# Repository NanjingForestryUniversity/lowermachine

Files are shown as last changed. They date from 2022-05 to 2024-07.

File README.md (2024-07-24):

# 下位机

下位机按上位机指令根据传送带脉冲等触发相机，完成棉花异性纤维的分选任务。采用的硬件是[Alinx](https://www.alinx.com/)的AC7Z100C ZYNQ开发板。

本IO扩展版提供了

- xxxxxx

接线时，12V电源连接到IO扩展板的电源接口，相机线应连接相机触发接口`TRIG1`、`TRIG2`和对应的`GND`接口，编码器线应连接在编码器输入接口`E1`和对应的`GND`接口，物体传感器应连接输入接口`E3`和对应的`GND`接口。注意底板不连接任何外部电源。

开发和部署说明见[doc/develop_and_deploy.md](doc/develop_and_deploy.md)

## 目录结构

- doc为说明文档，包括开发和部署细节、硬件设计的描述等

  - [develop_and_deploy.md](doc/develop_and_deploy.md)为开发和部署说明，首先看这个文档
  - [hardware_description.md](doc/hardware_description.md)为PL端逻辑设计说明，阐述了硬件工作的整体流程
  - [pl_reference_mannual.md](doc/pl_reference_mannual.md)为PL端逻辑在AXI总线上映射的寄存器参考手册
  - [sim_uppermachine_manual.md](doc/sim_uppermachine_manual.md)为模拟上位机运行的参考手册

- script为配置系统、安装环境、安装可执行文件、卸载可执行文件等的脚本

  关于脚本的使用，见[doc/develop_and_deploy.md](doc/develop_and_deploy.md)

  - target.sh为嵌入式linux中自动启动应用程序脚本

  - load\*.sh为嵌入式linux中加载驱动的脚本
  - .bashrc为嵌入式linux中配置环境变量的脚本

- protocol为上位机和下位机通信的协议

- hardware下位机主板、接口板、底板等的硬件设计

  - pl_platform为PL端硬件设计
  - xme0724ioextend为IO叠板的原理图和PCB

- source为AC7Z100C板子上运行的源程序和模拟上位机程序

  - liunx_app为Linux上运行的应用程序，即业务逻辑
  - linux_driver为Linux上的驱动，用于控制自定义的PL端硬件，其中drv_test结尾的目录为相应驱动模块的测试应用程序
  - petalinux_config为petalinux工具在编译u-boot、kernel、rootfs前进行的配置
  - petalinux_devicetree为本次自定义的Linux设备树文件部分，其余设备树为自动生成的
  - petalinux_hwdescription为petalinux所使用的硬件描述文件，包含了vivado工程中的比特流等信息
  - sim_uppermachine_manul为基于pyside6所编写的软件，用于模拟上位机发送指令，方便调试

## 版本

由于经常有不同类型的新要求出现，比如分选糖果、分选烟梗、同为糖果也具有不同的参数，因此不同的下位机型号（注意不是更新，比如同一台机器需要设置新的参数）应建立不同的分支，**主分支无实际意义**

分支命名规则（不使用中文，小写无空格）

```shell
b分支编号-p生产环境项目名-t分选对象[-其他特点1[-其他特点2...]]
```

中括号在这里表示可省略的项，中括号本身不应出现在实际命名中，其他特点应字母打头，可有多个，"-"相连

使用Git的tag功能定义版本（注意连着tag一起push），Github仓库的release功能同步发布最新版本

版本号遵循定义如下（不使用中文，小写无空格）

```shell
b分支编号-d文档版本-hPCB设计版本-lFPGA设计版本-p协议版本-s脚本版本-aAPP代码版本-i驱动版本-c系统编译配置版本-e设备树版本
```

分支编号和分支命名中编号一致。各部分版本应在相应目录下创建文件注明，比如`2.1`版本的PCB设计：PCB工程目录中建立`version`文本文件，内容为文本`2.1`。对于涉及整体设计的大改动版本号加`1`，其余改动版本号加`0.1`。每个分支的版本各自独立，新分支的版本从`1.0`起计算，也可从建立分支处原有版本起计算

##  作者

作者徐耀，随时欢迎师弟师妹7x24提着示波器的来问问题，联系方式：QQ：1170701029；微信：CeRnYool。

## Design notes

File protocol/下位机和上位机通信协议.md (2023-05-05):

# 下位机和上位机通信协议 V1.4

工作在OSI5~7层，单播TCP/IP。下位机控制阀，为客户端；上位机负责识别，为服务端

- 灵活利用类型字段实际值区分数据和指令
- 安全高效的长度定义，应对TCP/IP分粘包特性
- 字符序列形式简洁直观，方便抓包调试

## 流程

下位机上电后40s完成启动，初始处于停止状态。

要开始分选，下位机应处于停止状态，上位机先设置各个相机触发周期对应的编码器脉冲数，然后发送开始分选指令

收到开始分选指令后，下位机进入正在分选状态，依据编码器脉冲和设定，触发相机拍摄

上位机发送停止分选指令时，下位机应处于正在分选状态，下位机收到后停止读入编码器脉冲和触发相机，并进入停止状态。停止状态下下位机忽略收到的喷阀数据

## 格式

一包数据由8'haa打头，8'hbb结束，共6个字段：

| 起始  | 长度1 | 长度2 | 长度3 | 长度4 | 类型1 | 类型2 | 数据1 | 数据2 | ...  | 数据$i$ | 校验1 | 校验2 | 结束  |
| :---: | :---: | :---: | :---: | :---: | :---: | :---: | :---: | :---: | :--: | :-----: | :---: | :---: | :---: |
| 8'haa | 8'hzz | 8'hzz | 8'hzz | 8'hzz | 8'hzz | 8'hzz | 8'hzz | 8'hzz | ...  |  8'hzz  | 8'hff | 8'hff | 8'hbb |

### 起始&结束

起始为1字节，8'haa；结束为1字节，8'hbb

### 校验&长度

校验为2字节，`校验1`为8'hff，`校验2`为8'hff

长度为一个32位无符号数length，长度 = 数据字节数$i + 2$ <br>`长度1`指length[31:24]，`长度2`指length[23:16]，`长度3`指length[15:8]，`长度4`指length[7:0]

### 类型&数据

类型为ASCII字符序列，比如`类型1`为's'，`类型2`为't'代表开始分选命令<br>数据为ASCII字符序列或原始数据

**开始分选指令**<br>`类型1`为's'，`类型2`为't'，length为3，数据1固定为8'hff，具体如下：

| 起始  | 长度1 | 长度2 | 长度3 | 长度4 | 类型1 | 类型2 | 数据1 | 校验1 | 校验2 | 结束  |
| :---: | :---: | :---: | :---: | :---: | :---: | :---: | :---: | :---: | :---: | :---: |
| 8'haa | 8'd0  | 8'd0  | 8'd0  | 8'd3  |  's'  |  't'  | 8'hff | 8'hff | 8'hff | 8'hbb |

**停止分选指令**<br>`类型1`为's'，`类型2`为'p'，length为3，数据固定为8'hff，具体如下：

| 起始  | 长度1 | 长度2 | 长度3 | 长度4 | 类型1 | 类型2 | 数据1 | 校验1 | 校验2 | 结束  |
| :---: | :---: | :---: | :---: | :---: | :---: | :---: | :---: | :---: | :---: | :---: |
| 8'haa | 8'd0  | 8'd0  | 8'd0  | 8'd3  |  's'  |  'p'  | 8'hff | 8'hff | 8'hff | 8'hbb |

**设置相机触发周期对应的编码器脉冲数**<br>对于相机a，`类型1`为'p'，`类型2`为'a'，length为10，数据为十进制的ASCII字符序列，不足补'0'，比如'0''0''0''0''0''2''3''1'表示每231个编码器脉冲触发一次相机：

| 起始  | 长度1 | 长度2 | 长度3 | 长度4 | 类型1 | 类型2 | 数据1 | ...  | 数据7 | 数据8 | 校验1 | 校验2 | 结束  |
| ----- | ----- | ----- | ----- | ----- | ----- | ----- | ----- | ---- | ----- | ----- | ----- | ----- | ----- |
| 8'haa | 8'd0  | 8'd0  | 8'd0  | 8'd10 | 'p' | 'a' | '0' | ...  | '3' | '1' | 8'hff | 8'hff | 8'hbb |

对于相机b，`类型1`为'p'，`类型2`为'b'，其余字节含义和用法与相机a一致

对于相机c，`类型1`为'p'，`类型2`为'c'，其余字节含义和用法与相机a一致

对于相机d，`类型1`为'p'，`类型2`为'd'，其余字节含义和用法与相机a一致

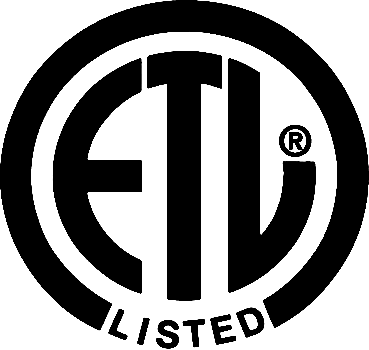
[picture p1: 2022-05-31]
hardware/ac7z100cioextend/res/etl.png

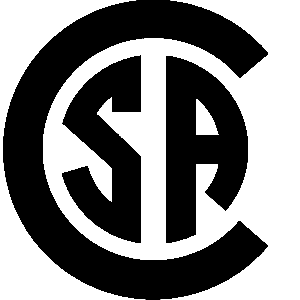
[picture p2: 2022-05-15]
hardware/ac7z100cioextend/res/csa.png

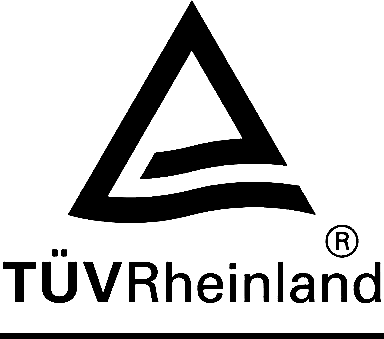
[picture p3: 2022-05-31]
hardware/ac7z100cioextend/res/tuv.png

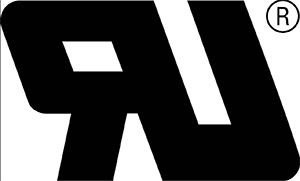
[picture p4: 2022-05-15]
hardware/ac7z100cioextend/res/ul.png

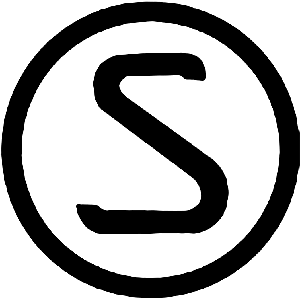
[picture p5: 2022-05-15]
hardware/ac7z100cioextend/res/semko.png

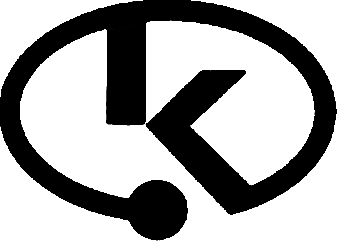
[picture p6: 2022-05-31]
hardware/ac7z100cioextend/res/ekmark.png

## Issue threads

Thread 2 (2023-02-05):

糖果分选机开始分选后传送带变速打不准

3703781, 2023-02-05:
这个版本[b01-d0.1-h1.0-p1.0-s0.1-a1.0](https://github.com/NanjingForestryUniversity/lowermachine/tree/b01-d0.1-h1.0-p1.0-s0.1-a1.0)
糖果分选机开始分选后传送带变速打不准
下面是维尔斯卢工的原话：
> 慢速调到能打了，做标记。调节到最快，打不到，再调到原先的慢速，也打不到，打的位置和快速一样的位置。停止分选，再开始分选，又能打到了。再调快打不准，再回原位也打不准，必须再停，再开。

3703781, 2023-02-05:
2023.02.06 过奕任、程磊、薛胜、吴旻会到维尔斯出差解决

3703781, 2023-02-08:
原因是传送带速度太快，相机触发频率较高，上位机算法不能及时计算出结果
在这个版本[b01-d0.2-h1.1-p1.0-s1.0-a1.1](https://github.com/NanjingForestryUniversity/lowermachine/tree/b01-d0.2-h1.1-p1.0-s1.0-a1.1)中，当存储上位机的图像数据队列为空时，将会给上位机发送报错信息。上位机收到后可以重新开始分选。同时让卢工固定传送带速度到约1m/s。

Chenglei98, 2023-02-08:
收到，miaow

&nbsp;

------------------&nbsp;原始邮件&nbsp;------------------
发件人:                                                                                                                        "NanjingForestryUniversity/lowermachine"                                                                                    ***@***.***&gt;;
发送时间:&nbsp;2023年2月8日(星期三) 晚上9:06
***@***.***&gt;;
***@***.******@***.***&gt;;
主题:&nbsp;Re: [NanjingForestryUniversity/lowermachine] 糖果分选机开始分选后传送带变速打不准 (Issue #2)

原因是传送带速度太快，相机触发频率较高，上位机算法不能及时计算出结果
 在这个版本b01-d0.2-h1.1-p1.0-s1.0-a1.1中，当存储上位机的图像数据队列为空时，将会给上位机发送报错信息。上位机收到后可以重新开始分选。同时让卢工固定传送带速度到约1m/s。

—
Reply to this email directly, view it on GitHub, or unsubscribe.
You are receiving this because you were assigned.Message ID: ***@***.***&gt;

Closed 2023-02-08.

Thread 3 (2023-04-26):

关于刘英老师的刨花板缺陷检测和分选

laiyz11, 2023-04-26:
刘老师的刨花板项目需要我们进行相机触发以及使用光电开关检测是否有木板在拍摄区域，具体要求是：
有木板在拍摄区域则需要依据编码器脉冲触发相机拍摄；
如果没有木板在拍摄区域则停止相机的触发脉冲；
需要同时触发多台相机

3703781, 2023-04-26:
已经新建分支 [b03-pwoodsorting-tchipboard1](https://github.com/NanjingForestryUniversity/lowermachine/tree/b03-pwoodsorting-tchipboard1)，用于这个项目

Closed 2023-04-28.

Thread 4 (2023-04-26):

b03分支刨花板项目需求和方案

3703781, 2023-04-26:
需求
1. 至少2路相机触发
2. 可以根据物体传感器的开关量，控制是否开启相机触发

具体方案：
1. ioextend板上，硬件支持4路相机触发，全部在PL端的encoder模块中实现，要可以设置独立的分频值
2. 因此需要更新与上位机的通信协议、应用程序、驱动程序来设置4个分频值
3. 有一个外部输入作为的开关A，同时有内部的寄存器作为开关B，内部寄存器C用来选择应用A还是A && B，作为encoder模块的复位rst_n信号

3703781, 2023-04-28:
方案1和3已在pl端实现，同时更新了linux驱动 commit https://github.com/NanjingForestryUniversity/lowermachine/commit/faae3829556e7d801b73d890738cfa37960489d9

3703781, 2023-05-27:
方案2已实现，见 commit https://github.com/NanjingForestryUniversity/lowermachine/commit/6449ebeeac16702461d9059ca8b319fef11e728c

Closed 2023-05-27.

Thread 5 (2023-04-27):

b03分支 PL端WNS高

3703781, 2023-04-27:
[b03](https://github.com/NanjingForestryUniversity/lowermachine/tree/b03-pwoodsorting-tchipboard1) 分支具体问题暂时没空查，帮忙查一下 @lyz55

3703781, 2023-05-27:
原工程中藏了好几个ila核，却没有显示在block design里，是以前在block design里添加的，然后在界面上删掉后实际还是参与了综合实现。重构工程后问题解决，已提交commit https://github.com/NanjingForestryUniversity/lowermachine/commit/faae3829556e7d801b73d890738cfa37960489d9

Closed 2023-05-27.

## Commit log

2022-05-15 original version
    [Sheet.SchDoc, Sheet1.SchDoc, xme0724ioextend.PrjPcb]
2022-05-31 change pcb to v2.0
    [Sheet.SchDoc, Sheet1.SchDoc, xme0724ioextend.PrjPcb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]
2022-07-03 寒假前烟梗分选机上已经开始用的
    测试能否打中暂时没啥问题，但溜的急，没充分测试
    [kernel.cfg, regs.xlsx, xme0724ioextend_v2.0_bom.xlsx]
2022-07-03 添加了版本描述
    tag中版本号遵循定义如下：
    b分支编号-d文档版本-hPCB设计版本-lFPGA设计版本-p协议版本-s脚本版本-aAPP代码版本-i驱动版本-c系统编译配置版本-e设备树版本
    分支编号和分支命名中编号一致。各部分版本应在相应目录下创建文件注明，比如`2.1`版本的PCB设计：PCB工程目录中建立`version`文本文件，内容为文本`2.1`。对于涉及整体设计的大改动版本号加`1`，其余改动版本号加`0.1`。每个分支的版本各自独立，新分支的版本从`1.0`起计算
2022-07-18 修正配置和命令
    1. rootfs中去掉packagegroup-core-ssh-dropbear
    2. rootfs中添加which和ncurses
    3. 部分echo改成echo -e
    4. 添加了set +H命令
2022-07-19 添加ENCODER中CLR位的补充说明
    1. 添加ENCODER中CLR位的补充说明
    2. 修正了一个错字
2022-08-01 更新了通信协议
    通信协议中添加了支持第二个fifo的命令
2022-09-01 机器已经部署到淮安
    8月底出差告一段落，运行一切正常
    1. 添加了喷阀数据队列走空计数和自动补偿功能
    2. 喷阀数据队列发生不可恢复的异常时向上位机报告错误
    3. 取消双FIFO
    [regs.xlsx]
2023-04-26 feat(pl,drv): 实现了4路相机的独立触发输出
    1. 修改了encoder模块的PL端设计和驱动，修改为为4路相机的独立触发输出
    2. 修改了启动方式，将比特流文件从BOOT.BIN中分离，实现PL端逻辑的动态加载
    BREAKING CHANGE: encoder模块的PL逻辑和linux驱动有变化，驱动的write接收参数从
    struct {
    unsigned int valve_divide_value;
    unsigned int camera_divide_value;
    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
    [regs.xlsx]
2023-04-26 test(drv): 增加对encoder驱动的测试应用程序
    encoder驱动的测试应用程序为source/linux_driver/encoder_drv_test
2023-04-26 feat(pl,drv): 添加了外部信号屏蔽相机触发的机制
    1. pl端的encoder模块实现了可选的外部复位信号
    2. pl端修改encoder模块的ENCODER_CR寄存器复位值，为仅限内部复位以及内部默认处于复位状态
    3. 驱动层实现外部复位的开启和关闭功能，驱动open时退出默认的复位清零状态
    由于驱动程序已在open时退出复位状态，应用程序可不做更改，驱动程序close后不会自动切换回复位状态
    4. 更新了驱动测试应用程序
    [regs.xlsx]
2023-04-27 fix(doc,drv,pl): 修正了ENCODER_CR的CLR位逻辑错误 1. 修正了pl_reference_mannual.md中的错误描述 2. 修正了encoder驱动中open和release函数对CLR位的设置 3. 修正了pl端encoder模块的ENCODER_CR寄存器复位值，使其默认为清除缓存状态
2023-04-28 refactor(pl,drv,doc,scr): 补充pl端源码
    1. 添加pl端vivado工程生成脚本和源码
    2. pl端设计删除本项目无关的fifo和valve interfaces模块
    3. 系统部署脚本中删除fifo相关内容
    4. 删除linux下的fifo驱动
    5. 修改与上述内容有关的文档
    BREAKING CHANGE: fifo有关功能和寄存器不再有效
    [regs.xlsx]
2023-05-05 refactor(pro): 升级了上位机和下位机的通信协议
    1. 长度字段增加到4个字节表示
    2. 去除了涉及喷阀等的无关描述和未使用的命令
    3. 修改了设置相机触发对应的脉冲数的命令，使得能够适应更多的相机数量
    4. 添加了下位机工作流程与通信有关的描述
    BREAKING CHANGE: 需要修改上位机以及下位机的应用程序，否则不能通信
2023-05-27 refactor(app, drv): 移植下位机的应用程序到新的通信协议 1. 应用程序实现了心跳包 2. 应用程序实现了4个相机的单独设置 3. 应用程序去除了有关喷阀、接收处理mask和硬件fifo相关的代码 4. 删除了fifo相关驱动程序 5. 修正了encoder驱动程序中的清除缓存逻辑
2023-06-20 feat(app): 新增了模拟上位机的软件程序
    1. 新增了模拟上位机软件，方便调试下位机
    2. 编写了模拟上位机的使用说明文档
    3. 修改了README的相关部分
2024-05-07 feat: migrate from the wood project to form the framework of this cotton project
    readme.md needs to be improved
    [PCB.PcbDoc, Sheet.SchDoc, kernel.cfg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]
2024-05-10 feat: Merge Library Files and add new hardware project readme.md needs to be updated hardware sch files needs to be corrected
    [01_ZYNQ_POWER.SchDoc, 03_ZYNQ_JTAG_BOOT.SchDoc, 04_ZYNQ_MISC_INTERFACE.SchDoc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]
